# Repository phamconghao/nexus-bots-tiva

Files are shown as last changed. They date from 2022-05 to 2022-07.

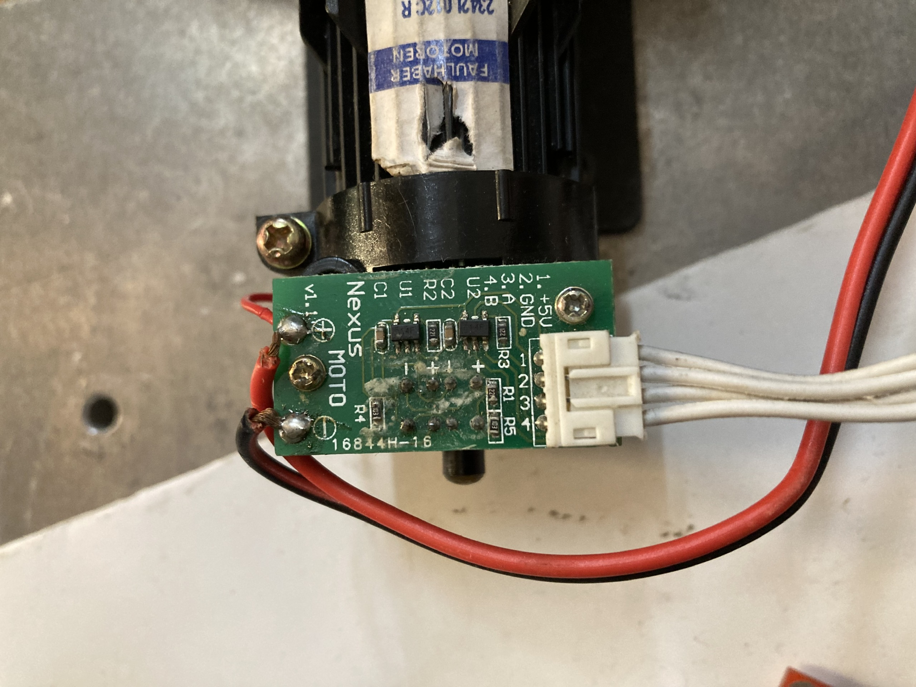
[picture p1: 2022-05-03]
docs/resources/enc.jpg

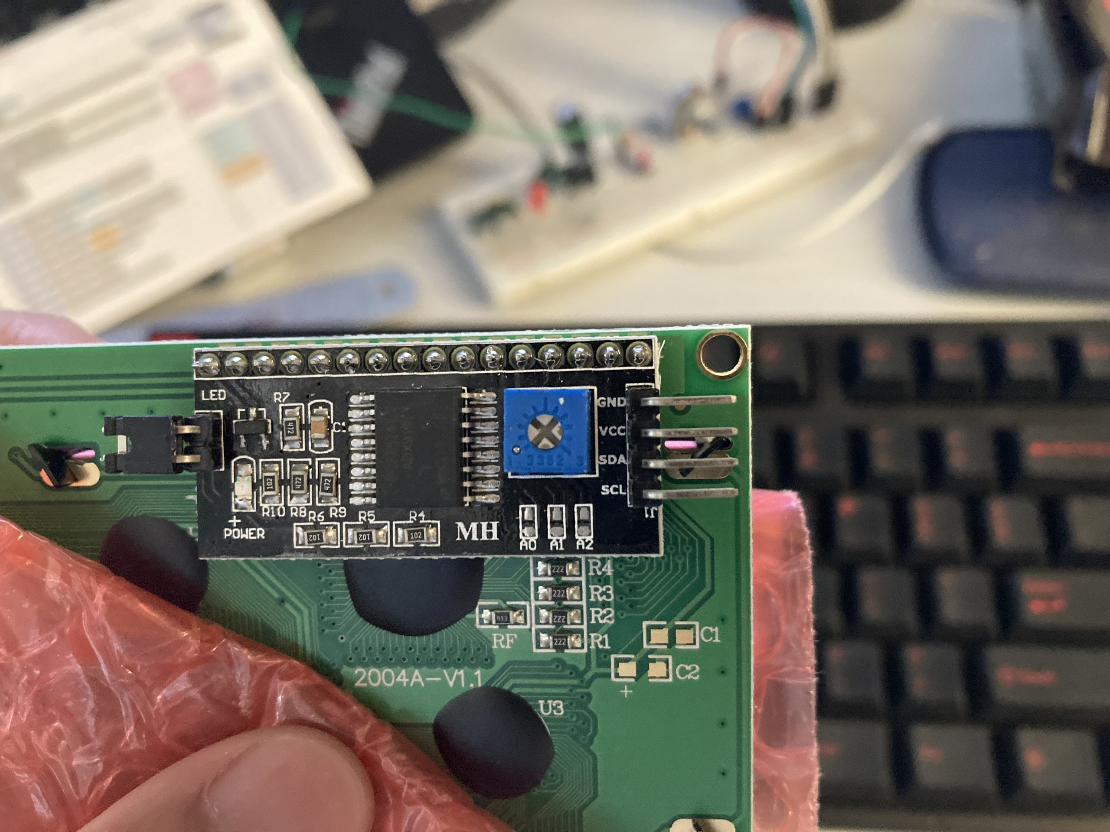
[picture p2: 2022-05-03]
docs/resources/lcd_i2c.jpg

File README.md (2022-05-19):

# Nexus Robot Controller Project for TI Tiva TM4C123
## nexus-bots-tiva
---

## Prerequisites
### Hardware
- Tiva C Launchpad TM4C123
- Nexus robot controller Board with BoosterPack Compatible
- Motor driver: VNH2SP30
- IMU: BMX160
- LCD 20x4
- Nexus robot base

### Software
- Arduino framework with Titiva platform in PlatformIO
- Firmware flashing tool OpenOCD

---

## Firmware features
** To enable demo mode, un-comment DEMO macro in [firmware/include/demo.h](https://github.com/khuehm17/nexus-bots-tiva/blob/main/firmware/include/demo.h), or vice sera. **
### Simple Demo
1. LED Blink Demo: 
	- ledBlink_demo();
2. LED Blink with PWM Demo: 
	- ledBlinkPWM_demo();
3. External IO Interrupt Demo: 
	- externalInterrupt_demo();
4. Serial Debug Printf Demo: 
	- dbgPrintf_demo();
5. PID Motor Control Demo: 
	- pidMotorControl_demo();
6. Timer Interrupt Demo: 
	- tmrInterrupt_demo(void);
	- TimerInterruptDemo_Handler();
7. ROS communication Demo: 
	- ros_PubSub_demo();
8. IMU Demo: 
	- bmx160_demo();
9. LCD i2c Demo:
	- lcd16x2_I2CLCD_demo();

### Nexus robot autonomous control

---

## Documentation
- Hardware schematic: docs/schematic_v1.0.pdf
- Pin diagram: docs/pin_diagram.pdf
- Software diagram: docs/software_digram/html-docs/index.html

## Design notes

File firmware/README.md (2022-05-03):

# nexus-bots-tiva
---
```
    This is a small implementation to port Nexus control program from AVR to Tiva C platform with the combination of ROSserial.
    Beside that, there are some simple demo of basic example.
```
## Platform
- Tiva C TM4C123
- Arduino framework with PlatformIO extension on VSCode
- ROS Noetic on Ubuntu 20.04 LTS

## Implemented Demo

### 1. LED Blink Demo
Blink the built-in LED on the Tiva C board with period 500ms.

** Implemented functions: 
  - void ledBlink_demo();
### 2. LED Blink with PWM Demo
Blink the built-in LED on the Tiva C board with period 500ms with fade-in and fade-out feature.

** Implemented functions: 
  - void ledBlinkPWM_demo();
### 3. External IO Interrupt Demo
Demonstration of External IO interrupt with Tiva C on-board button SW1.

** Implemented functions: 
  - void externalInterrupt_demo();
  - void extInterruptDemoHandler();
### 4. Serial Debug Printf Demo

### 5. PID Motor Control Demo

### 6. Timer Interrupt Demo

### 7. ROS communication Demo

After uploading firmware to Tiva, on ROS PC (with installed rosserial package), run bellow command:
```
    $ roscore
    $ rosrun rosserial_python serial_node.py /dev/ttyACM0 _baud:=115200
    $ rostopic echo tiva_chatter
    $ rostopic pub toggle_led std_msgs/Empty --once
```

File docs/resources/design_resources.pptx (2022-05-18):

## Tiva Robot Controller Board

Design resources

## Tiva C LaunchPad Dimensions

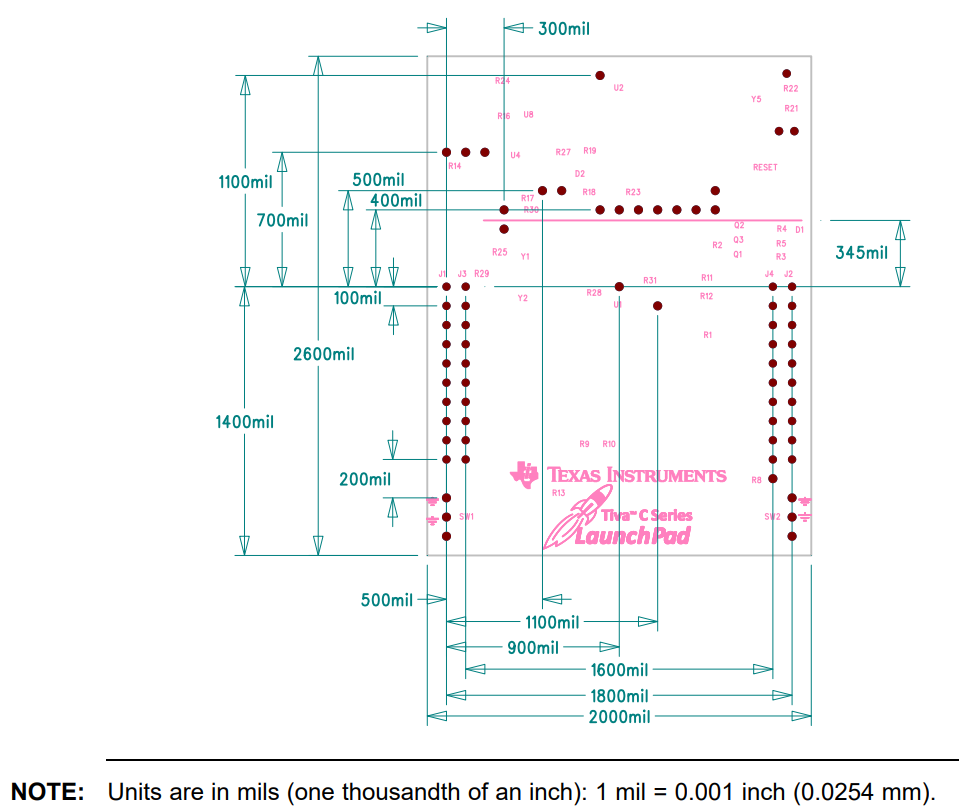
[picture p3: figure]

https://www.ti.com/lit/ug/spmu296/spmu296.pdf

## RS485 Module Dimensions

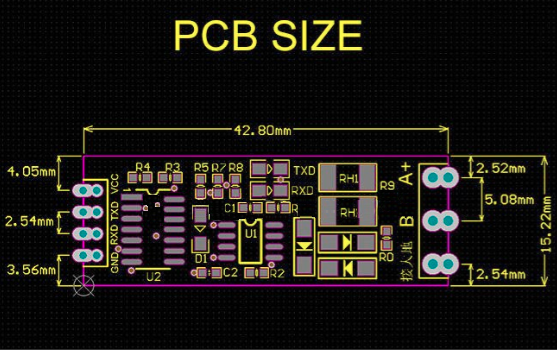
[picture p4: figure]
Không có mô tả.
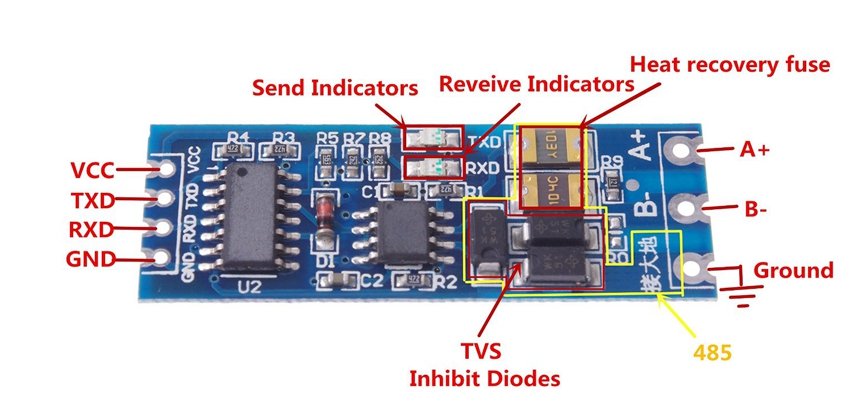
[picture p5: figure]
Mạch chuyển giao tiếp UART TTL to RS485 V2 – Hshop.vn

## RS485 Pins

+ ： +5V DC Power +5V
- ： GND Ground
A ： A RS485 A(+)
B ： B RS485 B(-)

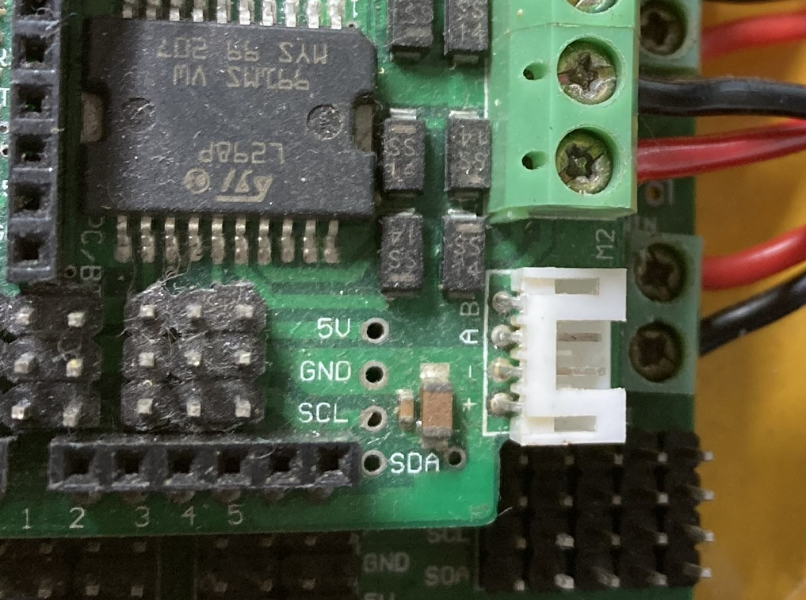
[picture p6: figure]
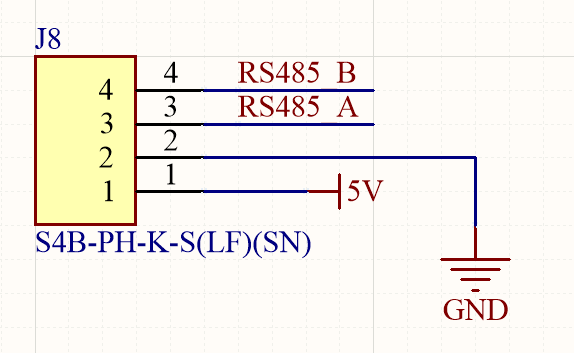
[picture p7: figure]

## Motor encoder Pins

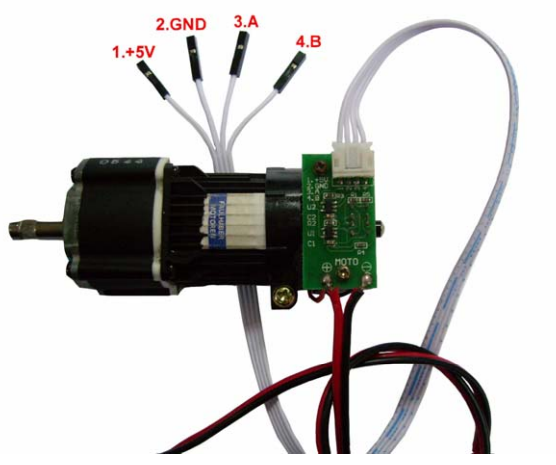
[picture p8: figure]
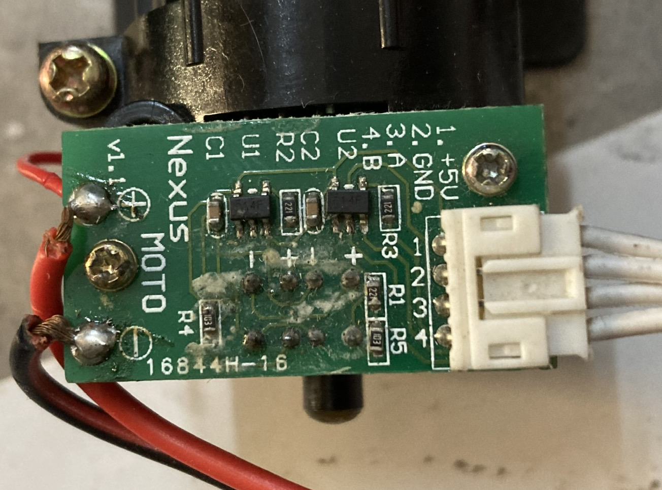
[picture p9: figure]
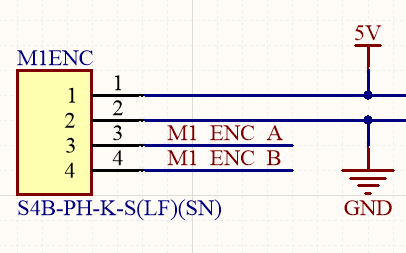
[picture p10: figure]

## LCD I2C Pins

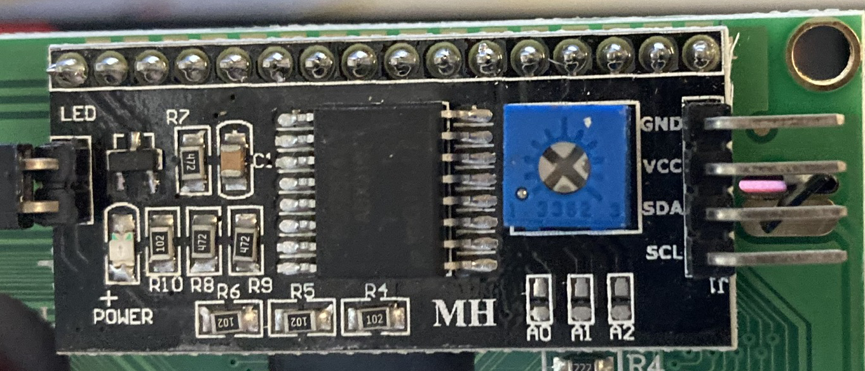
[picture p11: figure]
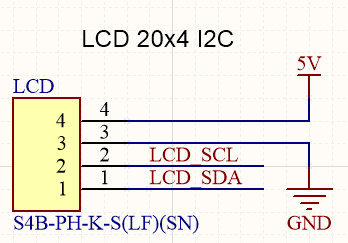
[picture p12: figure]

## BMX160 I2C Pins

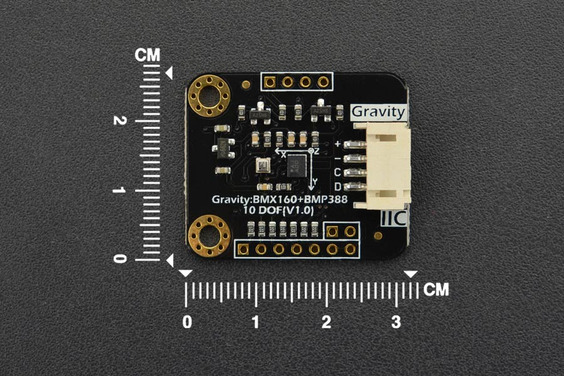
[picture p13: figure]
Gravity: BMX160+BMP388 10 DOF Sensor
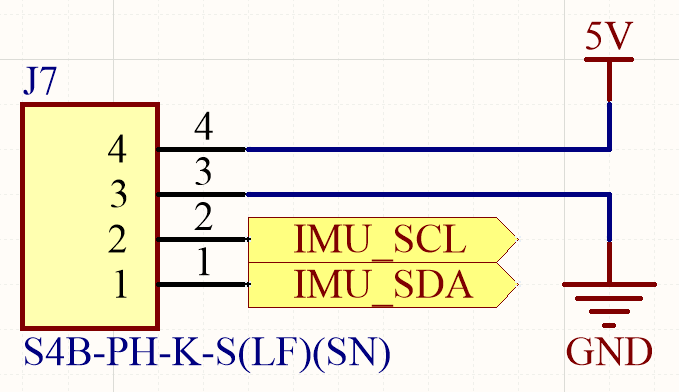
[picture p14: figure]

## S4B-PH-K-S(LF)(SN) Dimensions

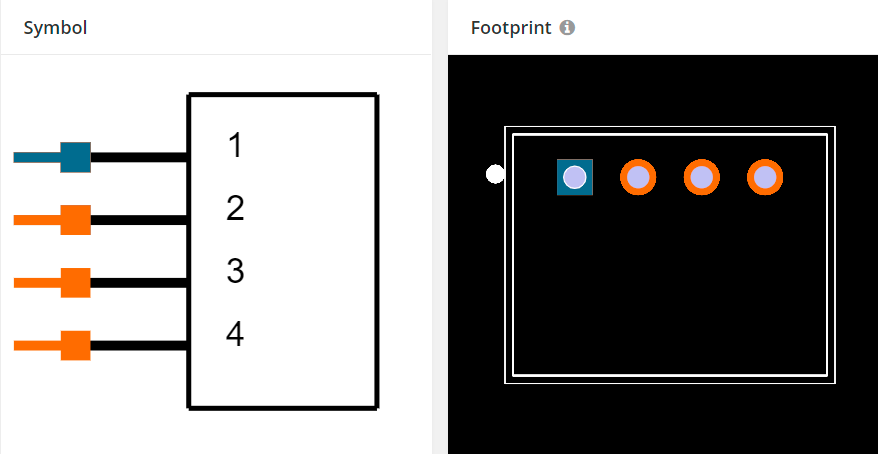
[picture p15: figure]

https://www.snapeda.com/parts/S4B-PH-K-S%28LF%29%28SN%29/JST%20Sales/view-part/

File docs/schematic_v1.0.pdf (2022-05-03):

# S4B-PH-K-S(LF)(SN) ADJ 1

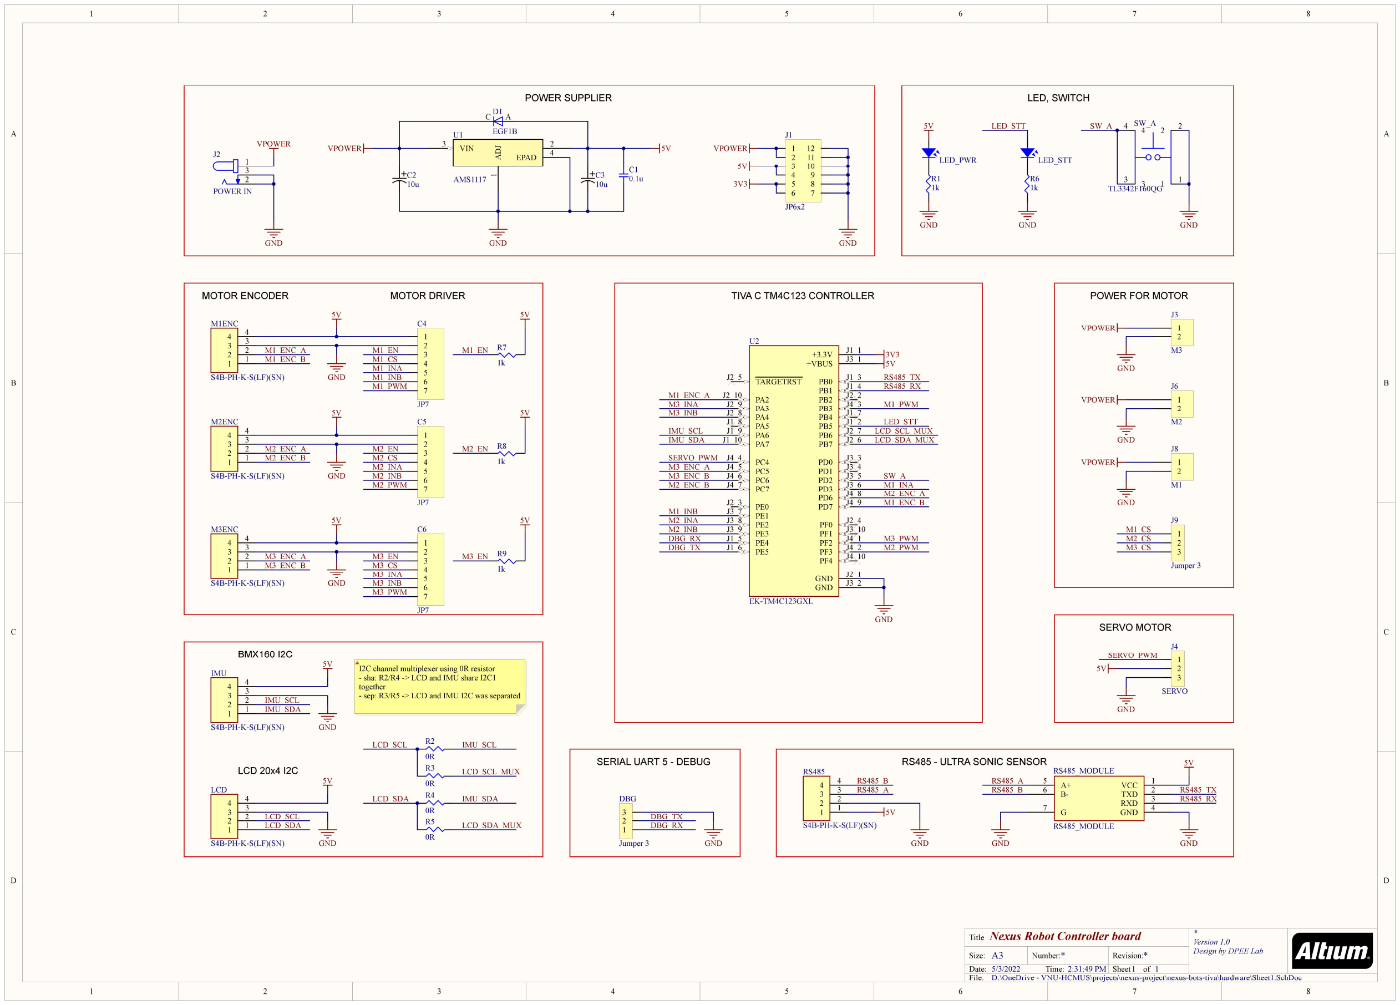
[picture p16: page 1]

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
Version 1.0
Design by DPEE Lab

1

## Nexus Robot Controller board

* | *
5/3/2022 | 2:31:49 PM
D:\OneDrive - VNU-HCMUS\projects\nexus-project\nexus-bots-tiva\hardware\Sheet1.SchDoc

Title

Size: | Number:
Date:
File:

Revision:
Time: | Sheet | of

A3

VPOWER

GND

VPOWER

GND

5V

5V

3V3

GND

C1
0.1u C2
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
VPOWER

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
M2ENC

S4B-PH-K-S(LF)(SN)

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
M3ENC

S4B-PH-K-S(LF)(SN)

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
### 2 VIN 3

EPAD 4

U1

AMS1117

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
JP6x2

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
Jumper 3

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
RS485

S4B-PH-K-S(LF)(SN)

VCC | 1
TXD | 2
RXD | 3
GND | 4

A+ 5
B- 6

G

7

RS485_MODULE

RS485_MODULE

GND

5V

RS485_A

RS485_B
RS485_B

RS485_A

GND

M1_ENC_A
M1_ENC_B

M2_ENC_B

M2_ENC_A

M3_ENC_A
M3_ENC_B

IMU_SCL
IMU_SDA

IMU_SDA

IMU_SCL

M2_ENC_B

M1_INB

M2_INB

M2_INA

RS485_TX
RS485_RX

M1_CS
M1_INA
M1_INB
M1_PWM

M2_CS
M2_INA
M2_INB
M2_PWM

M3_CS
M3_INA
M3_INB
M3_PWM

M1_CS
M2_CS
M3_CS

RS485_TX
RS485_RX

M1_PWM

M1_INA
M2_ENC_A

M3_PWM
M2_PWM

R1
1k

LED_PWR

5V

GND

### MOTOR ENCODER

### BMX160 I2C

### RS485 - ULTRA SONIC SENSOR

### POWER SUPPLIER

MOTOR DRIVER | TIVA C TM4C123 CONTROLLER

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
S4B-PH-K-S(LF)(SN)

LCD_SCL
LCD_SDA

### LCD 20x4 I2C

GND

DBG_TX
DBG_RX

### SERIAL UART 5 - DEBUG

R2
0R

LCD_SCL

R3
0R

IMU_SCL

LCD_SDA | R4
| 0R R5
| 0R

IMU_SDA

LCD_SDA_MUX

LCD_SCL_MUX

LCD_SCL_MUX
LCD_SDA_MUX

M3_INB

M3_INA

DBG_TX

DBG_RX

1
3
2

J2

POWER IN

VPOWER

GND

VPOWER

GND

VPOWER

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
Jumper 3

### POWER FOR MOTOR

C A

D1

EGF1B

TARGETRST J2_5

PA2 J2_10
PA3 J2_9
PA4 J2_8
PA5 J1_8
PA6 J1_9
PA7 J1_10

PC4 J4_4
PC5 J4_5
PC6 J4_6
PC7 J4_7

PE0 J2_3
PE1 J3_7
PE2 J3_8
PE3 J3_9
PE4 J1_5
PE5 J1_6
+3.3V | J1_1
+VBUS | J3_1
PB0 | J1_3
PB1 | J1_4
PB2 | J2_2
PB3 | J4_3
PB4 | J1_7
PB5 | J1_2
PB6 | J2_7
PB7 | J2_6
PD0 | J3_3
PD1 | J3_4
PD2 | J3_5
PD3 | J3_6
PD6 | J4_8
PD7 | J4_9
PF0 | J2_4
PF1 | J3_10
PF2 | J4_1
PF3 | J4_2
PF4 | J4_10
GND | J2_1
GND | J3_2

U2

EK-TM4C123GXL

R6
1k

LED_STT

GND

LED_STT

LED_STT

3

3
1

1

4

4
2

### 2 SW_A

TL3342F160QG

GND

SW_A

### LED, SWITCH

M1_EN

M2_EN

M3_EN

R7
1k

5V

M1_EN

R8
1k

5V

M2_EN

R9
1k

5V

M3_EN

SERVO_PWM

### SERVO MOTOR

1
2
3

J4

SERVO

5V

GND

SW_A

SERVO_PWM

M1_ENC_A

M1_ENC_B

M3_ENC_A
M3_ENC_B

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
M1ENC

S4B-PH-K-S(LF)(SN)

I2C channel multiplexer using 0R resistor
- sha: R2/R4 -> LCD and IMU share I2C1 together
- sep: R3/R5 -> LCD and IMU I2C was separated

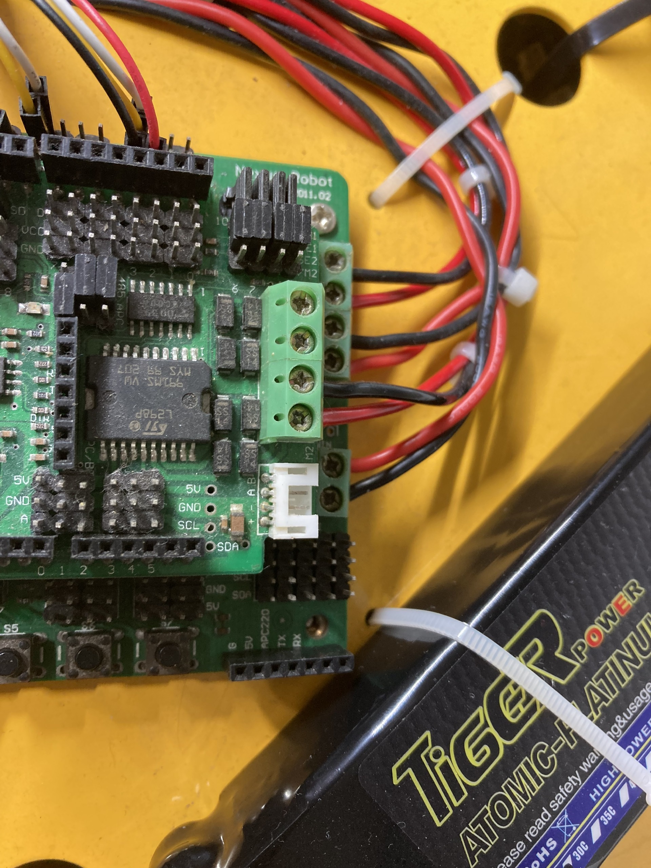
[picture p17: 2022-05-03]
docs/resources/rs485.jpg

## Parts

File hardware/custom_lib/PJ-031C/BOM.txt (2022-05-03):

3DX_CUI_DEVICES_Supplier: CUI Devices
3DX_CUI_DEVICES_Description: 1.3 x 4.2 mm, 2.0 A, Horizontal, Through Hole, Dc Power Jack Connector
3DX_CUI_DEVICES_Model Number: PJ-031D

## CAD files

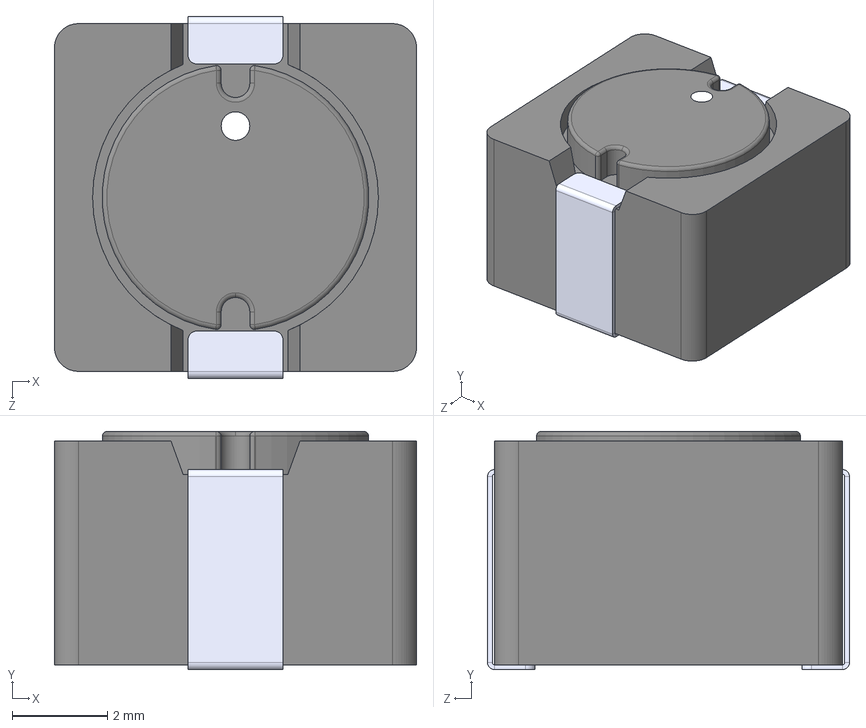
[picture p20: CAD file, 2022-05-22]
hardware/custom_lib/B1047AS-331M_P3/B1047AS-331M=P3.STEP
7.60 x 5.00 x 7.60 mm

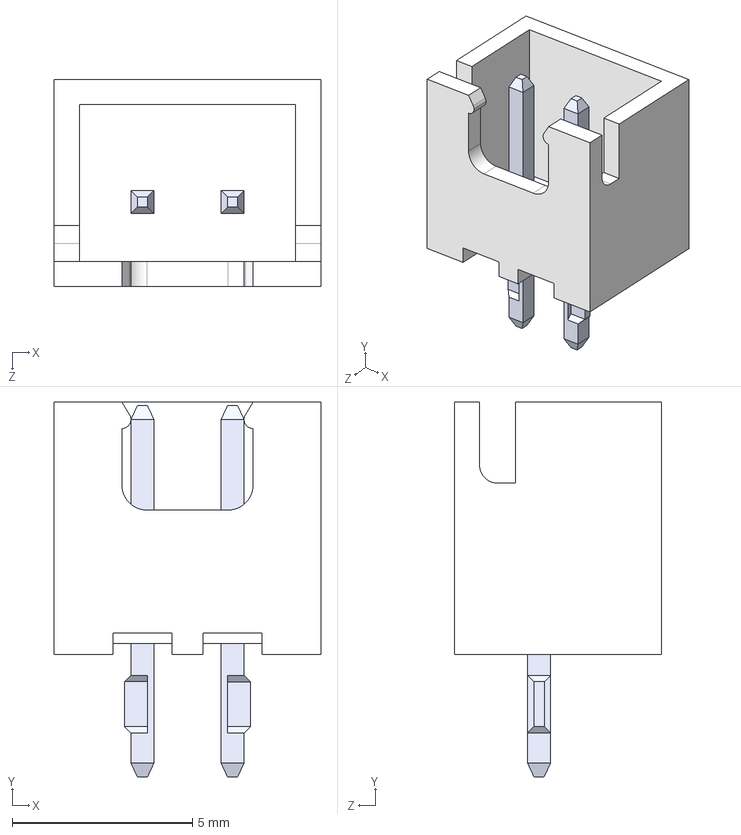
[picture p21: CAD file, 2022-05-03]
hardware/custom_lib/B2B-XH-A_LF__SN_/B2B-XH-A-LF--SN---3DModel-STEP-418109.STEP
7.40 x 10.4 x 5.75 mm

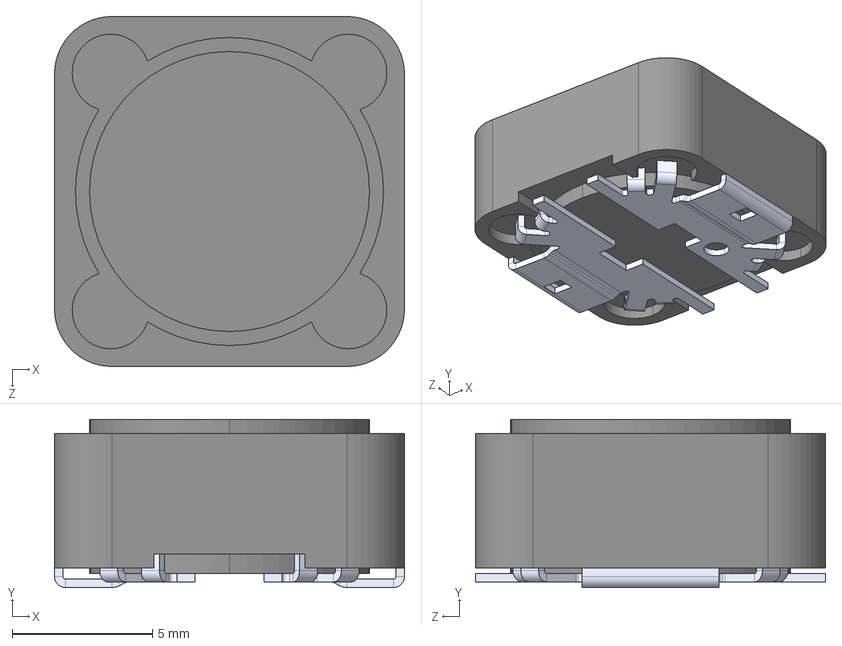
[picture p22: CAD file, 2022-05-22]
hardware/custom_lib/DR125-331-R/DR125-331-R.STEP
12.5 x 6.00 x 12.5 mm

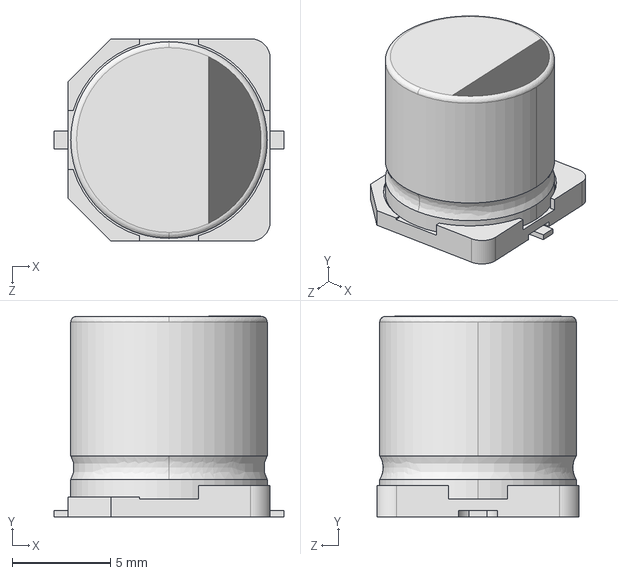
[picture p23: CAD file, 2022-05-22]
hardware/custom_lib/EEE2AA220P/EEE-2AA220P.STEP
11.7 x 10.2 x 10.3 mm

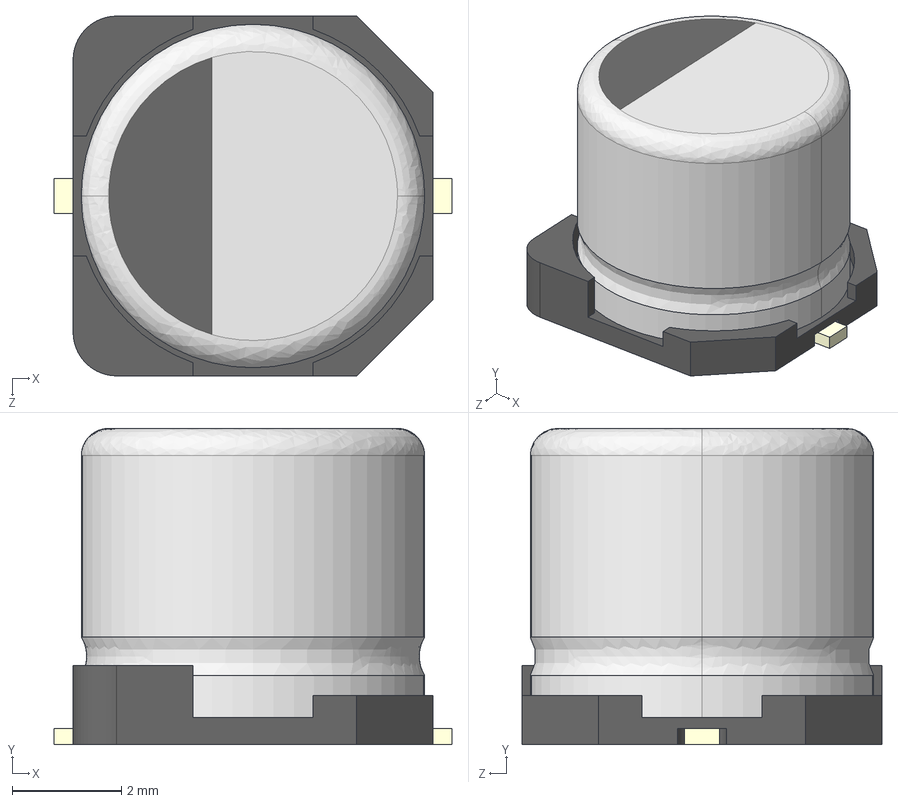
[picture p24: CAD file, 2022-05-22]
hardware/custom_lib/EEEHB1V220P/EEEHB1V220P.STEP
7.30 x 5.80 x 6.60 mm

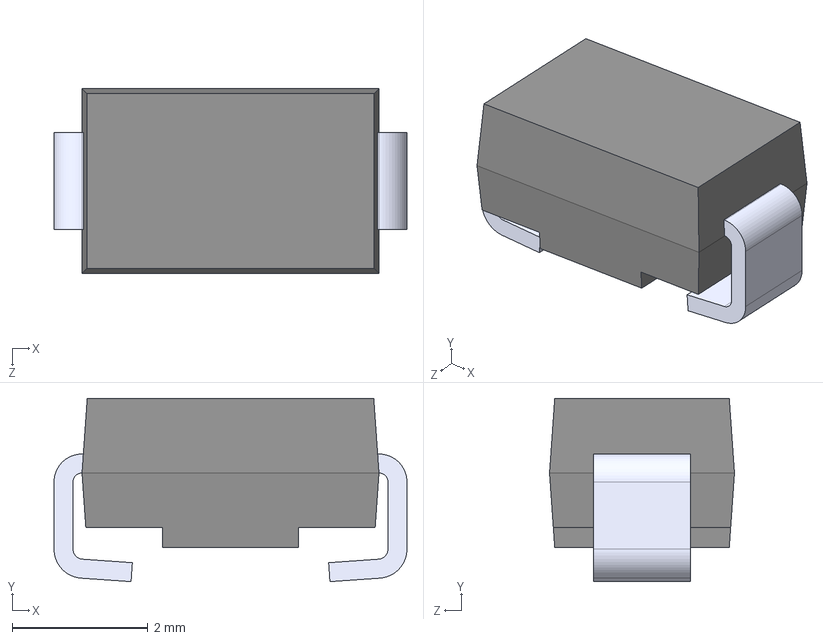
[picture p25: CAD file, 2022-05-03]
hardware/custom_lib/EGF1B/EGF1B.STEP
5.20 x 2.70 x 2.73 mm

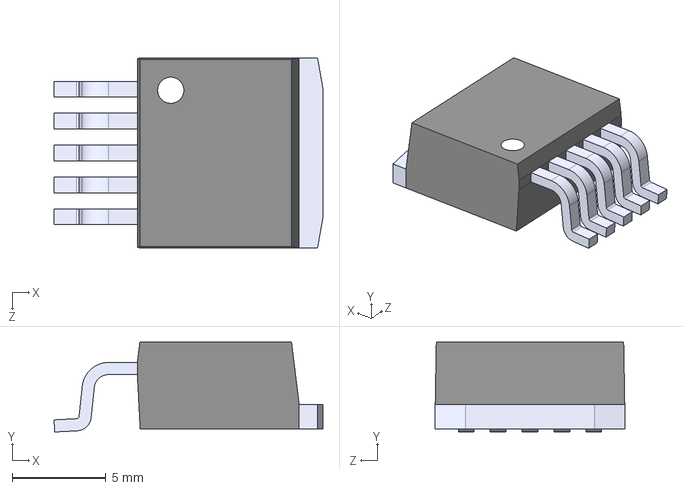
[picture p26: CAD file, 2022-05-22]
hardware/custom_lib/LM2596S-5/NOPB.STEP
14.4 x 4.80 x 10.2 mm

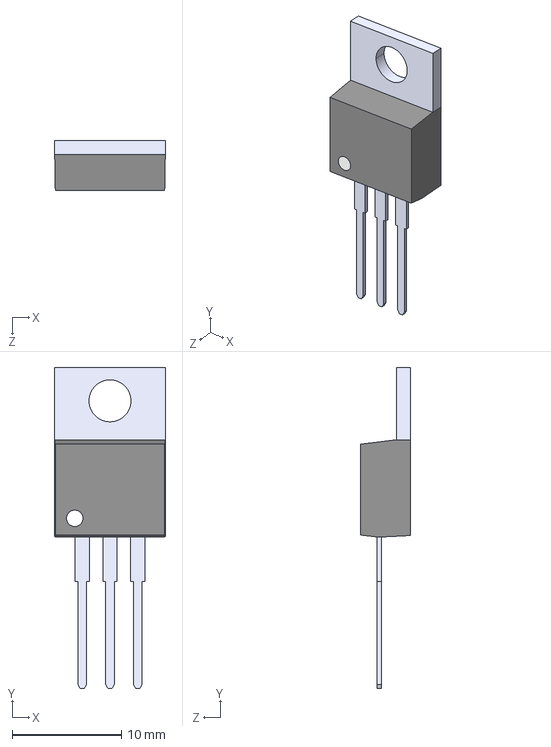
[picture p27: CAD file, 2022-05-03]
hardware/custom_lib/LM7805/LM7805--3DModel-STEP-56544.STEP
10.2 x 29.3 x 4.57 mm

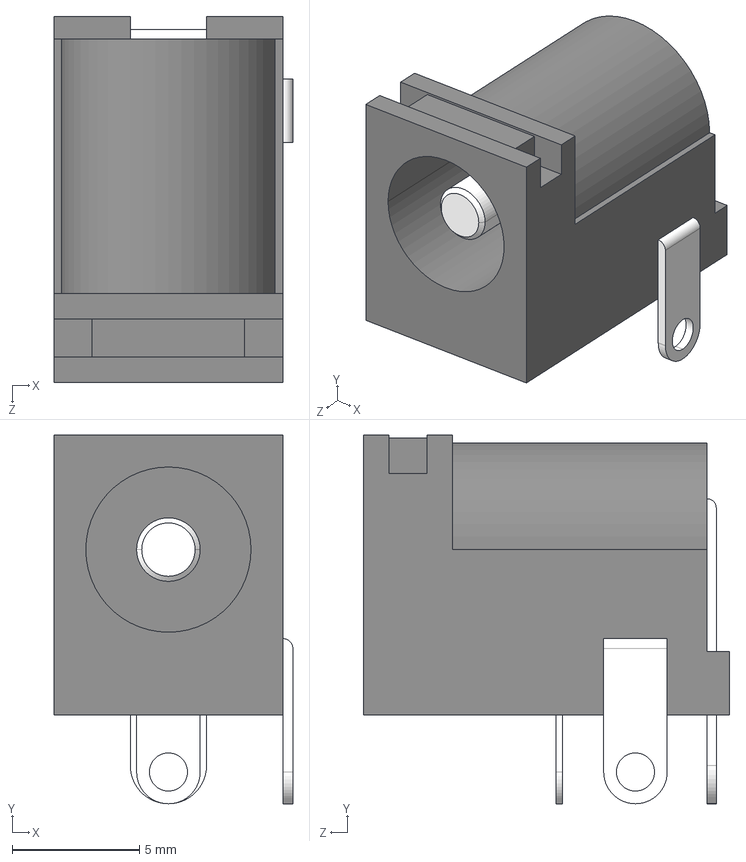
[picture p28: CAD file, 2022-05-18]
hardware/custom_lib/PJ-002B/PJ-002B--3DModel-STEP-56544.STEP
9.40 x 14.5 x 14.4 mm

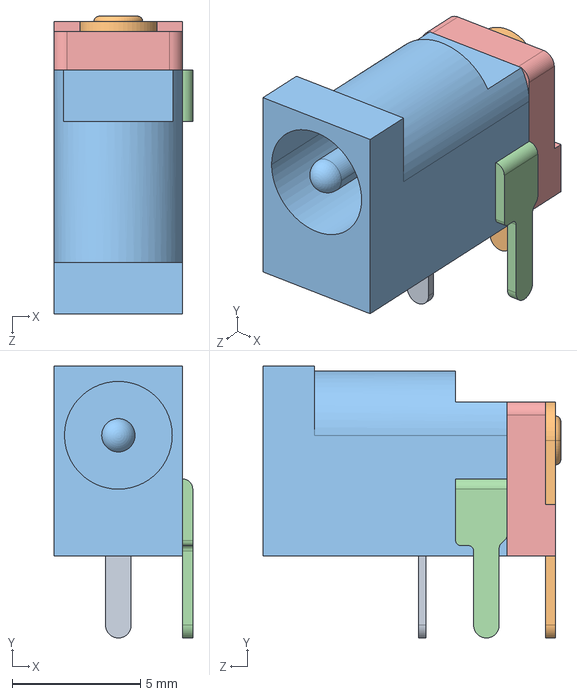
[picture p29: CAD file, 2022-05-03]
hardware/custom_lib/PJ-031C/CUI_DEVICES_PJ-031D.step
5.40 x 10.6 x 11.6 mm

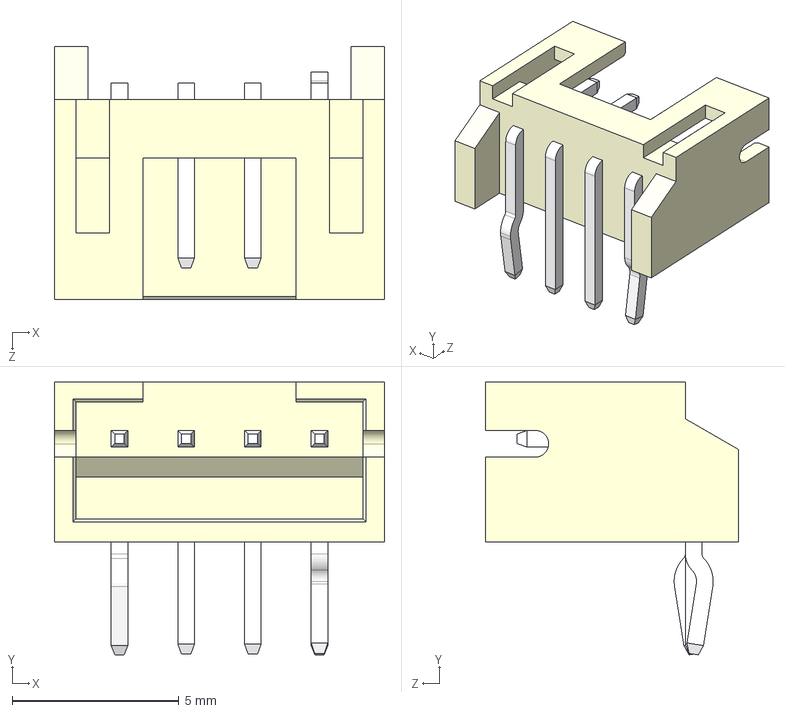
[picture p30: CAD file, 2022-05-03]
hardware/custom_lib/S4B-PH-K-S_LF__SN_/S4B-PH-K-S(LF)(SN)--3DModel-STEP-56544.STEP
9.90 x 8.18 x 7.60 mm

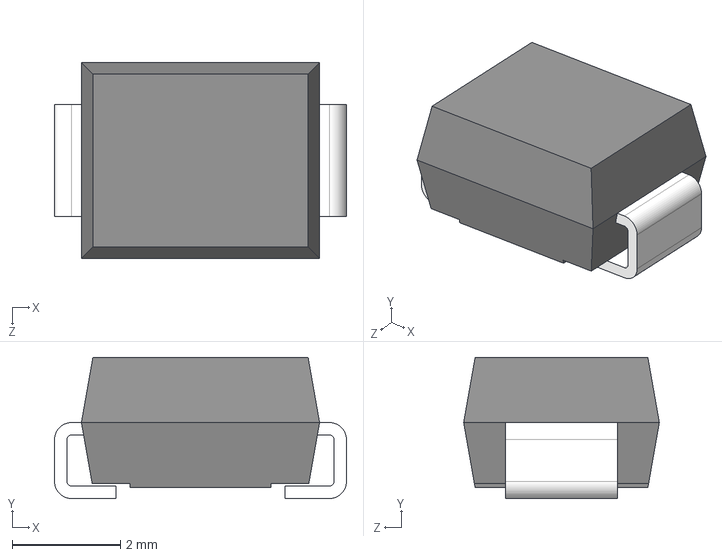
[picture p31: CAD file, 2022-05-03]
hardware/custom_lib/SMBJ28A/SMBJ28A.STEP
5.40 x 2.61 x 3.62 mm

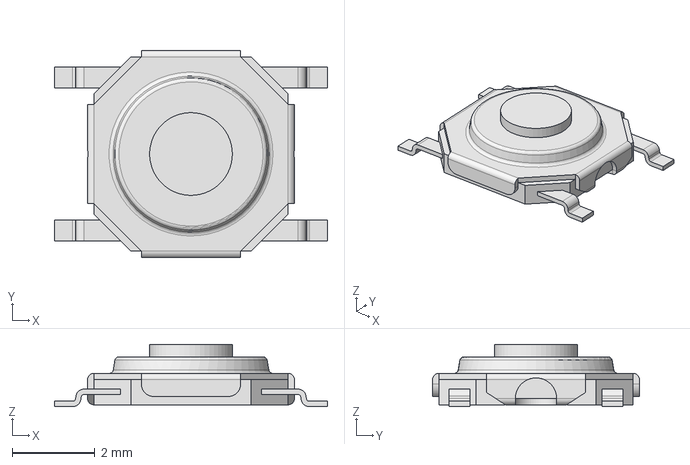
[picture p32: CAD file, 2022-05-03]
hardware/custom_lib/TL3342F160QG/TL3342F160QG--3DModel-STEP-520916.STEP
6.60 x 5.00 x 1.50 mm

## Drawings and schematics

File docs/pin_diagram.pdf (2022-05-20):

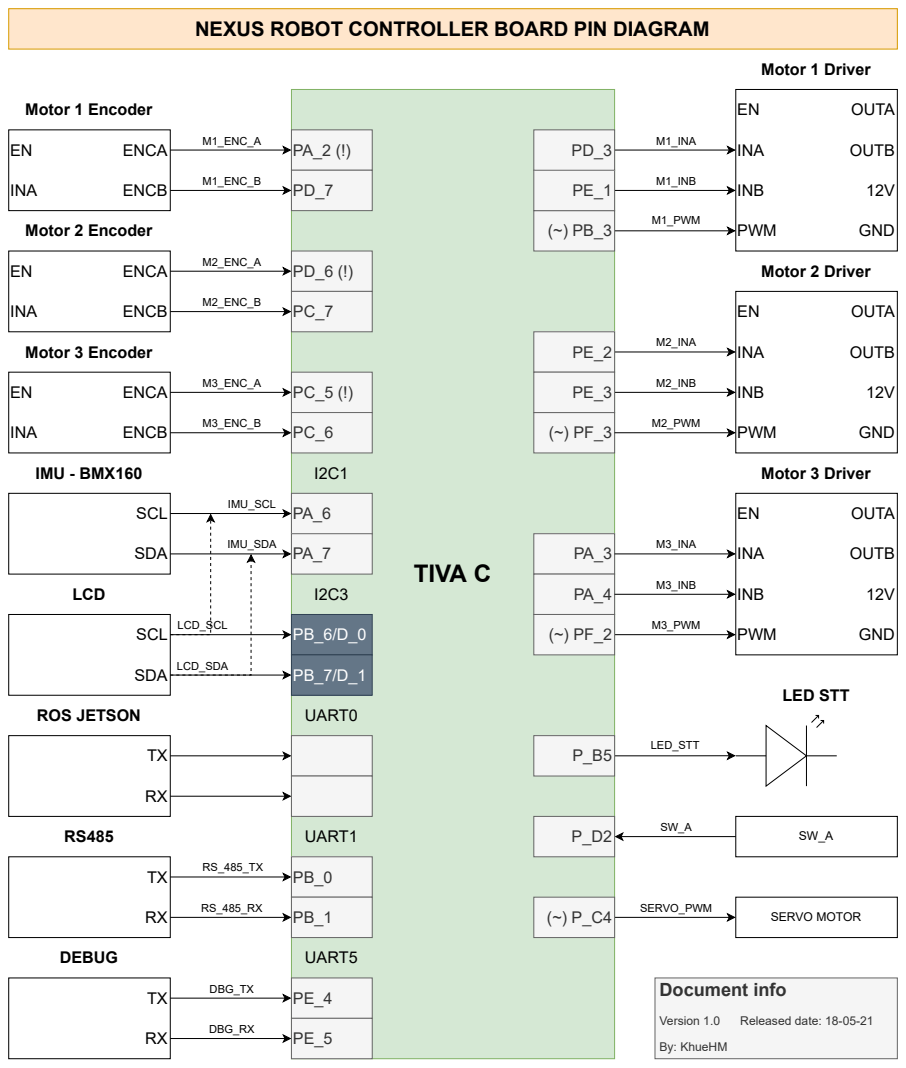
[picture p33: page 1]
TIVA C; INA; INB; PWM; OUTA; OUTB; GND; M1_PWM; M1_INA; M1_INB; GND M2_PWM; M2_INA; M2_INB; GND M3_PWM; M3_INA; M3_INB; M1_ENC_A ENCA; M1_ENC_B ENCB; M2_ENC_A ENCA; M2_ENC_B ENCB; M3_ENC_A ENCA; M3_ENC_B ENCB; Motor 1 Encoder; Motor 2 Encoder; Motor 3 Encoder; Motor 1 Driver; Motor 2 Driver; Motor 3 Driver; IMU_SCL SCL; IMU_SDA SDA; IMU - BMX160; LCD_SCL SCL; LCD_SDA SDA; LCD; ROS JETSON; UART0; UART1; DBG_TX TX; DBG_RX RX; DEBUG; UART5; LED_STT; LED STT; SERVO MOTOR; SERVO_PWM (~) P_C4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

NEXUS ROBOT CONTROLLER BOARD PIN DIAGRAM

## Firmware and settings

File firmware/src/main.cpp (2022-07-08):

/**
 *   @file  main.cpp
 *
 *   @brief
 *     Main implementation of the Nexus Demo
 */

/**************************************************************************
 *                            Include Files
 **************************************************************************/
/* Main Include Files */
#include "main.h"

/**************************************************************************
 *                           Global Declarations
 **************************************************************************/

/**
 *  Global Variable for Motor Wheel Back Encoder parameters
 */
Encoder_Params_t encoderWheel_Back_Params = {.Encoder_Handler = 
                                                encoderWheel_Back_Handler};
/**
 *  Global Variable for Motor Wheel Right Encoder parameters
 */
Encoder_Params_t encoderWheel_Right_Params = {.Encoder_Handler = 
                                                encoderWheel_Right_Handler};
/**
 *  Global Variable for Motor Wheel Left Encoder parameters
 */
Encoder_Params_t encoderWheel_Left_Params = {.Encoder_Handler = 
                                                encoderWheel_Left_Handler};

/**************************************************************************
 *                           Local Declarations
 **************************************************************************/

/**
 *  Wheel _Back_ object for control task
 */
MotorWheel motorWheel_Back(M1_PWM, M1_DIR_A, M1_DIR_B, M1_ENCA, M1_ENCB, 
                &encoderWheel_Back_Params,
                REDUCTION_RATIO_NAMIKI_MOTOR, WHEEL_CIRC);
/**
 *  Wheel _Right_ object for control task
 */
MotorWheel motorWheel_Right(M2_PWM, M2_DIR_A, M2_DIR_B, M2_ENCA, M2_ENCB, 
                &encoderWheel_Right_Params,
                REDUCTION_RATIO_NAMIKI_MOTOR, WHEEL_CIRC);
/**
 *  Wheel _Left_ object for control task
 */
MotorWheel motorWheel_Left(M3_PWM, M3_DIR_A, M3_DIR_B, M3_ENCA, M3_ENCB, 
                &encoderWheel_Left_Params,
                REDUCTION_RATIO_NAMIKI_MOTOR, WHEEL_CIRC);

/**
 *  Omni Nexus object for control task
 */
Omni3WD omniNexusBot(&motorWheel_Back, &motorWheel_Right, &motorWheel_Left);

/**
 *  Node handle object for communication task
 */
ros::NodeHandle h_Node;
ros::Subscriber<geometry_msgs::Twist> sub_velTwist("/cmd_vel", &cmdTwistSpeedCallback);
ros::Subscriber<geometry_msgs::PoseWithCovarianceStamped> sub_initPose("/initialpose", &initialPoseCallback);
// ros::Publisher pub_GyroAccel("imu/data_raw", &imu_GyroAccel_msg);
// ros::Publisher pub_Mag("imu/mag", &imu_Mag_msg);
ros::Publisher pub_Odom("/odom", &odom_msg);
// sensor_msgs::Imu imu_GyroAccel_msg;
// sensor_msgs::MagneticField imu_Mag_msg;
nav_msgs::Odometry odom_msg;
nav_msgs::Odometry odom_initpose;

/**
 *  IMU BMX160 handle object
 */
DFRobot_BMX160 bmx160;
sBmx160SensorData_t Omagn, Ogyro, Oaccel;

/**
 *  PCF8574 LCD handle object
 */
LiquidCrystal_PCF8574 lcd(LCD_I2C_ADDR);

/**
 *  Holonomic handle
 */
// holoOdom_t nexusHoloOdom;
int i = 0, j = 0;
float matrix_speed_wheels_encoder[3];
float matrix_w_b[3][3];
float matrix_b_w[3][3];
float robot_heading_inertial;
float robot_speed_inertial_frame[2]; 
float robot_speed_body_frame[2];
float omega;
float robot_position_inertial[2];
bool initialPoseReceived = false;


/**************************************************************************
 *                      Nexus Bot Demo MAIN Program
 **************************************************************************/
void hardware_Init()
{
    /* 
     * Init the STT LED on Nexus controller Board
     */
    pinMode(NEXUS_STT_LED, OUTPUT);

#if LCD_OPTION
    /* 
     * Init the hardware I2C LCD 
     */
    Wire.begin();
    Wire.beginTransmission(LCD_I2C_ADDR);

    if (Wire.endTransmission())
    {
        DEBUG_PRINTF("  LCD not found.\n");
    }
    else
    {
        DEBUG_PRINTF("  LCD found.\n");
        /* Initialize the LCD */
        lcd.begin(LCD_COLS_NUM, LCD_ROWS_NUM);
    }
#endif

#if IMU_OPTION
    /**
     * Init the hardware bmx160 IMU
     */
    while (bmx160.begin() != true)
    {
        DEBUG_PRINTF("Initialization faild, please check the I2C connect!\n");
        sttLED_Flash();
        delay(1000);
    }
#endif 

    /** Enable PID for object Omni Nexus */
    omniNexusBot.PIDEnable(KC, TAUI, TAUD, SAMPLETIME);
}

void main_program()
{
#ifdef DEBUG
    debug_init();
#endif

#ifdef DEMO     // --> For DEMO
    pinMode(NEXUS_STT_LED, OUTPUT);
    sttLED_Flash();

    // ledBlink_demo();
    // ledBlinkPWM_demo();
    // externalInterrupt_demo();
    // dbgPrintf_demo();
    // pidMotorControl_demo();
    // tmrInterrupt_demo();
    // ros_PubSub_demo();
    // bmx160_demo();
    // lcd16x2_I2CLCD_demo();
    // nexusControl_demo();
    ros_Odom_demo();

#else           // --> For MAIN Program
    unsigned long previous_time_ms = 0;
    unsigned long current_time_ms = 0;
    float delta_t = 0;
    unsigned long delta_t_ms = 0;

    DEBUG_PRINTF("Start MAIN Program\n");

    hardware_Init();

    /* Start PID Regulate Task, periodic with SAMPLETIME = 2ms or 500Hz freq */
    attachTimerInterrupt(PID_TIMER_BASE, PID_TIMER_SYSCTL_PERIPH, &PID_TimerInterrupt_Handler, 500);
#if IMU_OPTION
    /* Start Reading IMU Task, periodic with 100Hz frequency */
    attachTimerInterrupt(IMU_TIMER_BASE, IMU_TIMER_SYSCTL_PERIPH, &IMU_TimerInterrupt_Handler, 100);
#endif
    
    // Initialize position and pose of the robot before the robot works.
    odom_msg.pose.pose.position.x = 0.0;
    odom_msg.pose.pose.position.y = 0.0;
    odom_msg.pose.pose.position.z = 0.0;
    odom_msg.pose.pose.orientation.x = 0.0;
    odom_msg.pose.pose.orientation.y = 0.0;
    odom_msg.pose.pose.orientation.z = 0.0;
    odom_msg.pose.pose.orientation.w = 1.0;

    // generate_robot_body(matrix_wheel_robot);
    generate_matrix_wheel_body(matrix_w_b, matrix_b_w);
    
    h_Node.initNode();
    /* Subscribe velocity data from ROS */
    h_Node.subscribe(sub_velTwist);
    h_Node.subscribe(sub_initPose);
    
#if IMU_OPTION    
    h_Node.advertise(pub_GyroAccel);
    h_Node.advertise(pub_Mag);
#endif

    h_Node.advertise(pub_Odom);
    
    // omniNexusBot.setCarRotateLeft(5);
    // omniNexusBot.setCarRight(50);
    previous_time_ms = millis();

    /* Main loop */
    for (;;)
    {
#if IMU_OPTION
        /* Publish IMU data to ROS */
        pub_GyroAccel.publish(&imu_GyroAccel_msg);
        pub_Mag.publish(&imu_Mag_msg);
#endif

#if CAL_ODOM

        if (initialPoseReceived)
        {
            odom_msg.pose.pose.position.x += odom_initpose.pose.pose.position.x;
            odom_msg.pose.pose.position.y += odom_initpose.pose.pose.position.y;
            odom_msg.pose.pose.position.z += odom_initpose.pose.pose.position.z;
            odom_msg.pose.pose.orientation.z += odom_initpose.pose.pose.orientation.z;
            initialPoseReceived = false;
        }
        current_time_ms = millis();
        get_speed_body_frame_from_encoderMMPS(robot_speed_body_frame, &omega);
        delta_t_ms = current_time_ms - previous_time_ms;
        delta_t = (float)delta_t_ms / 1000;
        robot_transform_body_to_inertial(robot_heading_inertial, robot_speed_body_frame, robot_speed_inertial_frame);
        robot_integrate_speed(robot_position_inertial, &robot_heading_inertial, robot_speed_inertial_frame, omega, delta_t);
        previous_time_ms = current_time_ms;
        odom_msg.header.stamp = h_Node.now();
        // Since all odometry is 6DOF we'll need a quaternion created from yaw
        geometry_msgs::Quaternion odom_quater = tf::createQuaternionFromYaw(robot_heading_inertial);

        odom_msg.header.frame_id = "odom_p";
        odom_msg.child_frame_id = "base_footprint_p";
        // Set the position
        odom_msg.pose.pose.position.x = robot_position_inertial[0];
        odom_msg.pose.pose.position.y = robot_position_inertial[1];
        odom_msg.pose.pose.position.z = 0.0;
        odom_msg.pose.pose.orientation = odom_quater;
        // Set the velocity
        odom_msg.twist.twist.linear.x = robot_speed_inertial_frame[0];
        odom_msg.twist.twist.linear.y = robot_speed_inertial_frame[1];
        odom_msg.twist.twist.angular.z = robot_heading_inertial;

        sttLED_Flash();
        for (int i = 0; i < 36; i++)
        {
            if (i == 0 || i == 7)
            {
                odom_msg.pose.covariance[i] = 1e-3;
                odom_msg.twist.covariance[i] = 1e-3;
            }
            else if (i == 14 || i == 21 || i == 28)
            {
                odom_msg.pose.covariance[i] = 1e6;
                odom_msg.twist.covariance[i] = 1e6;
            }
            else if (i == 35)
            {
                odom_msg.pose.covariance[i] = 1e3;
                odom_msg.twist.covariance[i] = 1e3;
            }
            else
            {
                odom_msg.pose.covariance[i] = 0;
                odom_msg.twist.covariance[i] = 0;
            }
        }
        /* Publish Odom data to ROS */
        pub_Odom.publish(&odom_msg);
#endif
        h_Node.spinOnce();
        delay(5);
    }
#endif          // --> Endif DEMO
}

void attachTimerInterrupt(uint32_t ui32Base, uint32_t ui32Peripheral, void (*p_TmrHandler)(), unsigned int tmrFreq)
{
    // Timer Period calculation
    unsigned long ulPeriod = SysCtlClockGet() / tmrFreq;
    // Timer interrupt Configuration
    MAP_SysCtlPeripheralEnable(ui32Peripheral);
    MAP_TimerConfigure(ui32Base, TIMER_CFG_PERIODIC);
    MAP_TimerLoadSet(ui32Base, TIMER_A, ulPeriod - 1);
    TimerIntRegister(ui32Base, TIMER_A, p_TmrHandler);
    MAP_TimerIntEnable(ui32Base, TIMER_TIMA_TIMEOUT);
    MAP_TimerEnable(ui32Base, TIMER_A);
}

void sttLED_Flash(void)
{
    digitalWrite(NEXUS_STT_LED, HIGH);
    delay(50);
    digitalWrite(NEXUS_STT_LED, LOW);
    delay(50);
    digitalWrite(NEXUS_STT_LED, HIGH);
    delay(50);
    digitalWrite(NEXUS_STT_LED, LOW);
    digitalWrite(NEXUS_STT_LED, HIGH);
    delay(50);
    digitalWrite(NEXUS_STT_LED, LOW);
}

void cmdTwistSpeedCallback(const geometry_msgs::Twist& cmd_twistSpeed)
{
    robot_control_wheel(cmd_twistSpeed.linear.x, cmd_twistSpeed.angular.z);
}

void initialPoseCallback(const geometry_msgs::PoseWithCovarianceStamped& init_pose)
{
    odom_initpose.pose.pose.position.x = init_pose.pose.pose.position.x;
    odom_initpose.pose.pose.position.y = init_pose.pose.pose.position.y;
    odom_initpose.pose.pose.orientation.z = init_pose.pose.pose.orientation.z;
    odom_initpose.pose.pose.orientation.w = init_pose.pose.pose.orientation.w;
    initialPoseReceived = true;
}

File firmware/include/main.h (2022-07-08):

#ifndef MAIN_H
#define MAIN_H

/**************************************************************************
 *                            Include Files
 **************************************************************************/
/* Energia framework Include Files. */
#include "Energia.h"
/* Debug print Include Files */
#include "debug_printf.h"
/* Control Include Files: */
#include "hw_handler.h"
#include "MotorWheel.h"
#include "Omni3WD.h"
#include "holonomic.h"
// #include "holonomic_3wheel.h"
// Tiva C driver Include Files
#include "inc/hw_ints.h"
#include "inc/hw_memmap.h"
#include "driverlib/interrupt.h"
#include "driverlib/rom_map.h"
#include "driverlib/sysctl.h"
#include "driverlib/timer.h"
/* ROS Include Files */
#include <ros.h>
#include <std_msgs/String.h>
#include <std_msgs/Empty.h>
#include <geometry_msgs/Twist.h>
#include <sensor_msgs/Imu.h>
#include <sensor_msgs/MagneticField.h>
#include <nav_msgs/Odometry.h>
#include <tf/transform_broadcaster.h>
#include <geometry_msgs/Quaternion.h>
#include <geometry_msgs/PoseWithCovarianceStamped.h>
#include <geometry_msgs/PoseStamped.h>
#include <tf/tf.h>
#include <geometry_msgs/PoseStamped.h>
/* BMX160 Include Files */
#include <DFRobot_BMX160.h>
#include "MadgwickAHRS.h"
/* LCD I2C PCF8574 Include Files */
#include <LiquidCrystal_PCF8574.h>
#include <Wire.h>
/* Math Include Files */
#include <math.h>
#include <MatrixMath.h>
/* Demo Include Files */
#include "demo.h"

/**************************************************************************
 *                           Macros definition
 **************************************************************************/
/* Timer for scheduling periodic PID calculation */
#define IMU_TIMER_BASE              TIMER2_BASE
#define IMU_TIMER_SYSCTL_PERIPH     SYSCTL_PERIPH_TIMER2
/* Timer for scheduling periodic DEBUG print calculation */
#define DEBUG_TIMER_BASE            TIMER4_BASE
#define DEBUG_TIMER_SYSCTL_PERIPH   SYSCTL_PERIPH_TIMER4
/* Timer for scheduling periodic PID calculation */
#define PID_TIMER_BASE              TIMER5_BASE
#define PID_TIMER_SYSCTL_PERIPH     SYSCTL_PERIPH_TIMER5
#define TEST_

#ifndef MICRO_PER_SEC
    #define MICRO_PER_SEC 1000000
#endif

#define BODY_RADIUS                     150 // mm
#define REDUCTION_RATIO_NAMIKI_MOTOR    80
#define WHEEL_RADIUS                    50  // mm
#define WHEEL_CIRC                      (WHEEL_RADIUS * 2 * PI)

#define LCD_OPTION                      (0)
#define IMU_OPTION                      (0)
#define CAL_ODOM                        (1)


/* TIVA Board */
#define TIVA_RED_LED    PF_1
#define TIVA_BLUE_LED   PF_2
#define TIVA_GREEN_LED  PF_3
#define TIVA_SW1        PF_4
#define TIVA_SW2        PF_0

/* Nexus Control Breakout BoosterPack Board */
#define NEXUS_STT_LED   PB_5
#define NEXUS_SWA       PD_2

/* Motor 1 Pin Defs */
#define M1_PWM          PB_3
#define M1_DIR_A        PD_3
#define M1_DIR_B        PE_1
#define M1_ENCA         PD_7
#define M1_ENCB         PA_2

/* Motor 2 Pin Defs */
#define M2_PWM          PF_3
#define M2_DIR_A        PE_2
#define M2_DIR_B        PE_3
#define M2_ENCA         PC_7
#define M2_ENCB         PD_6

/* Motor 3 Pin Defs */
#define M3_PWM          PF_2
#define M3_DIR_A        PA_3
#define M3_DIR_B        PA_4
#define M3_ENCA         PC_5
#define M3_ENCB         PC_6

/* LCD I2C Defs */
#define LCD_I2C_ADDR    (0x27)
#define LCD_COLS_NUM    (16)
#define LCD_ROWS_NUM    (2)

/**************************************************************************
 *                           Global Declarations
 **************************************************************************/
extern Encoder_Params_t encoderWheel_Back_Params;
extern Encoder_Params_t encoderWheel_Right_Params;
extern Encoder_Params_t encoderWheel_Left_Params;

extern MotorWheel motorWheel_Back;
extern MotorWheel motorWheel_Right;
extern MotorWheel motorWheel_Left;

extern Omni3WD omniNexusBot;

extern ros::NodeHandle h_Node;
extern ros::Subscriber<geometry_msgs::Twist> sub_velTwist;
extern ros::Subscriber<geometry_msgs::PoseWithCovarianceStamped> sub_initPose;
// extern ros::Publisher pub_GyroAccel;
// extern ros::Publisher pub_Mag;
extern ros::Publisher pub_Odom;
// extern sensor_msgs::Imu imu_GyroAccel_msg;
// extern sensor_msgs::MagneticField imu_Mag_msg;
extern nav_msgs::Odometry odom_msg;
extern nav_msgs::Odometry odom_initpose;

extern TwoWire Wire2;
extern DFRobot_BMX160 bmx160;
extern sBmx160SensorData_t Omagn, Ogyro, Oaccel;

extern LiquidCrystal_PCF8574 lcd; // set the LCD address to 0x27 for a 16 chars and 2 line display

extern float matrix_speed_wheels_encoder[];
extern int i, j;
extern float matrix_w_b[3][3];
extern float matrix_b_w[3][3];
extern float robot_heading_inertial;
extern float robot_speed_inertial_frame[]; 
extern float robot_speed_body_frame[];
extern float omega;
extern float robot_position_inertial[];
extern bool initialPoseReceived;
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

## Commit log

2022-04-12 done ledBlink, ledBlinkPWM, extInterrupt demo
2022-04-12 modify Motor::debbuger()
2022-04-13 done get encoder speed (tested on hardware)
2022-04-13 fix error encoder results caused by printf
    [hw_handler.cpp]
2022-04-13 add debug print for encoder
2022-04-14 tested PID motor control on hardware
2022-04-15 add and tested timer interrupt (timer5)
2022-04-15 implement attachTimerInterrupt function
2022-04-15 done implementing new PID Regulating method (timer interrupt)
2022-04-15 update PID demo with interrupt timer debugger
2022-04-19 add encoder handler function to Motor class
2022-04-23 done IMU demo
2022-04-23 update PID lib
2022-04-23 add i2c LCD demo (tested with hardware)
2022-04-24 globalize IMU PID handler function
2022-05-03 add tiva Nexus controller board hardware design files
    [B2B-XH-A(LF)(SN).SchLib, B2B-XH-A-LF--SN---3DModel-STEP-418109.STEP, CUI_DEVICES_PJ-031D.step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]
2022-05-03 complete hardware design v1.0
    [Copy of PCB1.PcbDoc, PCB1.PcbDoc, PCB_Project1.PrjPCB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]
2022-05-03 update pcb hardware design v1.0
    [PCB1.PcbDoc, PCB_Project1.PrjPCB, Sheet1.SchDoc]
2022-05-18 fix errors due to DEMO pre-processor macro
    [demo.cpp, hw_handler.cpp, main.cpp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]
2022-05-18 release fabrication files v1.0
    [Copy of PCB1.PcbDoc]
2022-05-18 add new custom component lib
    [PJ-002B--3DModel-STEP-56544.STEP, SnapEDApcb.PcbLib, SnapEDAsch.SchLib]
2022-05-18 update design, fix v1.0 errors (issue #2)
    [PCB1.PcbDoc, PCB_Project1.PrjPCB, Sheet1.SchDoc]
2022-05-18 update Motor control Pin define for v1.0
2022-05-18 done test PID demo for single motor
2022-05-18 add PID regulate for wheel Right and Left
2022-05-19 update IMU demo i2c
2022-05-20 update pin diagram (tested with hardware)
2022-05-22 feat: add hardware component library
    add cap, inductor, lm2596s
    [B1047AS-331M=P3.STEP, B1047AS-331M=P3.SchLib, CAP_EEE2AA220P.PcbLib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]
2022-05-22 fix: update PCB hardware design, issue #2
    [PCB1.PcbDoc, PCB_Project1.PrjPCB, Sheet1.SchDoc]
2022-05-29 #update vel control from Jetson to umicro
2022-06-03 update IMU ros
2022-06-05 fix data Gyro IMU
    [hw_handler.cpp, main.h]
2022-06-15 Implement publish odometry ros demo
